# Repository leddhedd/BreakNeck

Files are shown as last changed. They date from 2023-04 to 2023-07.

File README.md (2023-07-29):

# The project formerly known as BreakNeck

<p align="center">
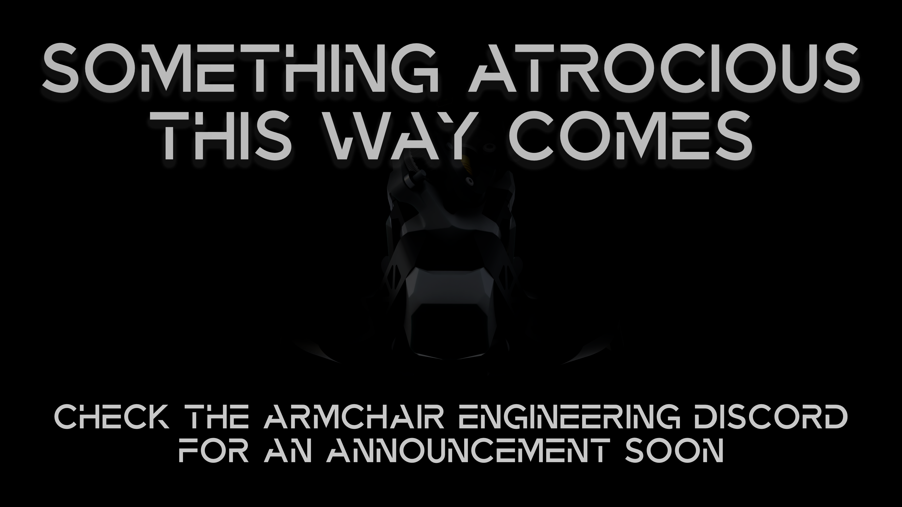
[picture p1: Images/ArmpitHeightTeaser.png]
  
</p>

Check out the Armchair Engineering Discord, and join the Breakneck User-Project ***[HERE](https://discord.com/channels/1029426383614648421/1071214081236816012)***

## THIS PROJECT HAS EVOLVED
BreakNeck is about to move over to the armchair engineering github, as well as undergoing some changes and additions.

## WE STAND ON THE SHOULDERS OF GIANTS

i want to give a particularly huge thanks to DoubleT, aTinyShellScript, Derpimus, Corvid, Zruncho, Maz, Kmobs, Smokescreens, Zackm0n, ohpvp, DWTas, ByThorsThunder, Frank.af, Kyleisah cBon, many of the members of the annex community and team, as well as many others for getting stuck in, test printing parts, and in some particularly idiotic cases, trialing, fitting and using the toolhead. the 3dp community wouldnt be what it is without the contibution and help of individuals like these, and i certainly wouldnt have completed the project to this level of polish without their help.

Huge thanks to all the guys over at the Armchair Engineering, Voron, and Annex discord for all the help and support in bringing this project together.

## What is this?

if you have stumbled across this repo, you are looking at the predecessor to **ARMPITHEIGHT** , i will leave the following description of what Breakneck was below for some back-lore.

Breakneck was a toolhead designed primarily for the Voron ecosystem, and any other front rail, front belt CoreXY Printer.
The main features and testing focus of the toolhead were remote air cooling, and a deliberate bend in the post-extruder filament path, for the purposes of inducing a bowden-like buffering effect.

## [> > > ASSEMBLY GUIDE < < <](https://github.com/leddhedd/BreakNeck/blob/main/Images/Assembly/Assembly-Instructions.md)

<p align="center">
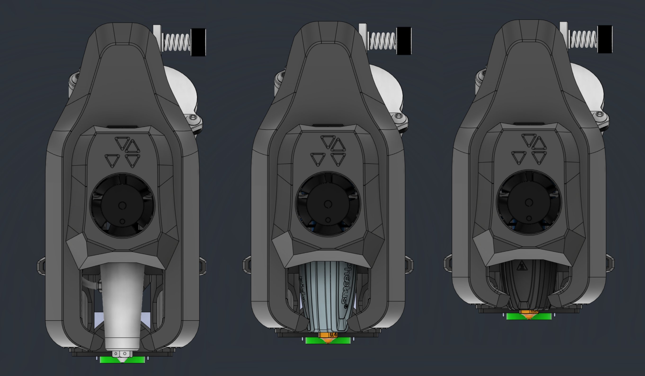
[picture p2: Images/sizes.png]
  
</p>

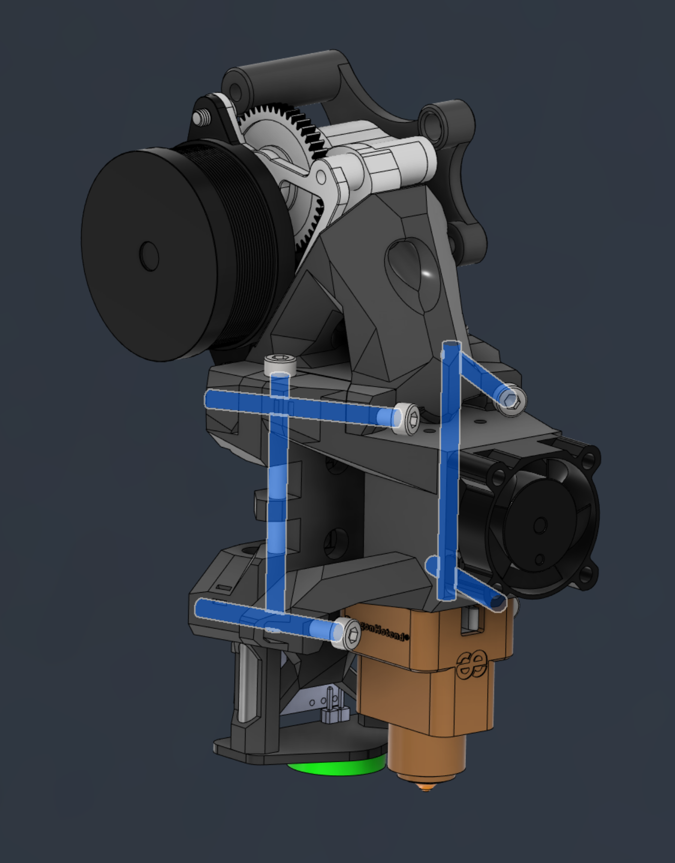
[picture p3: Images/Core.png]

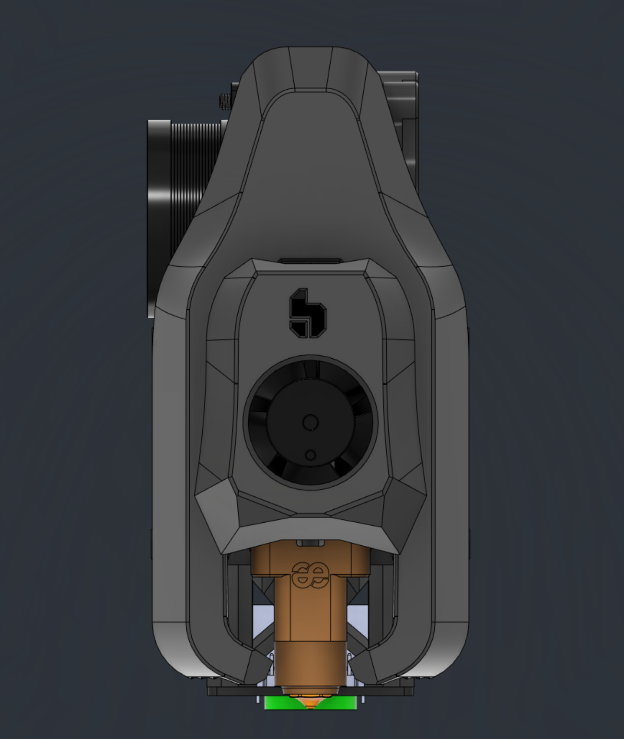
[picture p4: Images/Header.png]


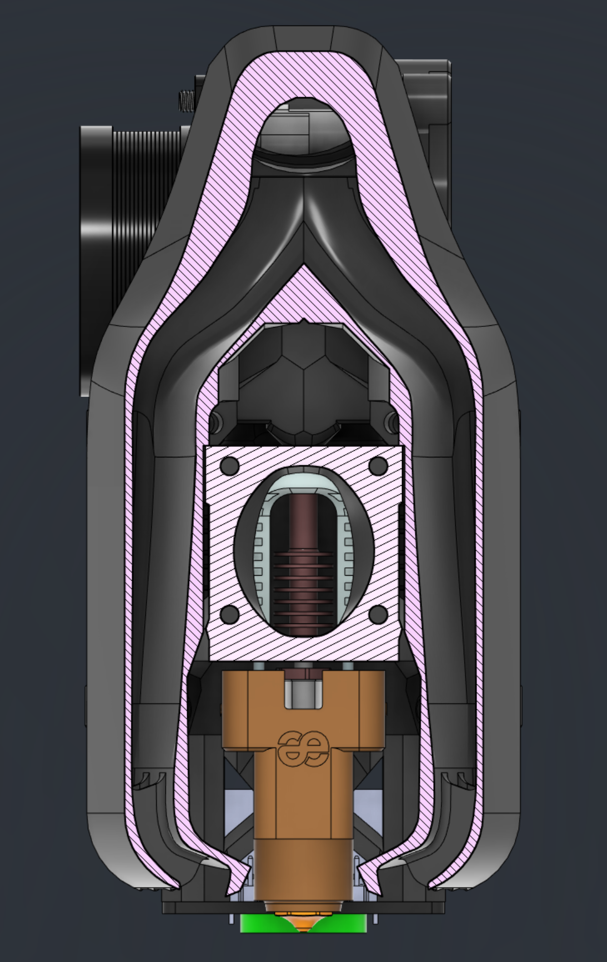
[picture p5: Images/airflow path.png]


Cpap cooling somewhat speaks for itself, its more cooling than you can typically get. more to come with updates, but the project focuses currently on 7040 blower fans commonly avaliable on AliExpress, and looking into small dyson hairdryer blower fans and other BLDC ducted fan options. As development continues, the focus will move away from the toolhead and more toward maximising performance from the remote fan whilst sourcing cheap and openly avaliable parts.

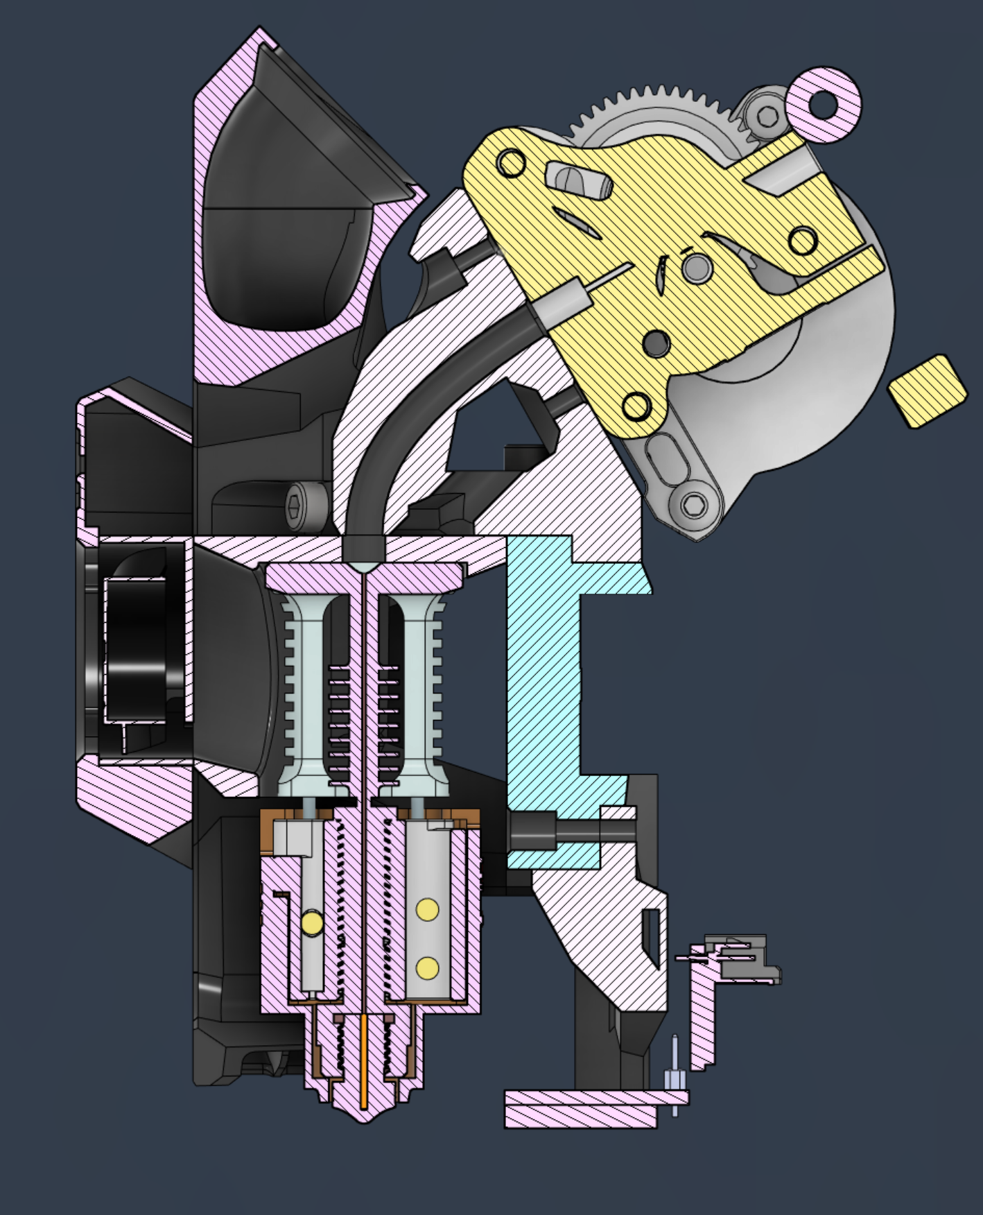
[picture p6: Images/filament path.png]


The post-extruder filament path bend is a solution to 2 problems, first is duct pathing is a nightmare with an extruder directly above the hotend, but most critically, bowden machines have been shown in several examples to produce cleaner walls and prints than direct drive machines. this effect comes at a tradeoff of course, with bowden machines having PA values that are essentially uncontrollable at high speed printing.
the filament path bend aims to create a small buffer of filament between the extruder and the hotend, in order to deliberately increase PA values and reduce the visibility of any extruder artifacting in the extruded lines.
The claims about bowden in general and easy to verify, and 24/7 printing has several videos, as well as MirageC on their efforts to reduce issue6 and VFA artifacting on their prints, with many commenters, and MrageC himself showing how clean a bowden machine can print when looking at this isolated artifact
in testing so far, the breakneck extruder mount seems to be producing a similar effect to the bowden tube, but keeping PA values much more in check than a full bowden system, allowing for more potential quality and less limitations on high-speed printing.

After Breakneck was tested thoroughly for a few months by various wonderful community members, it was decided to up the scope and try to provide the benefits of the above, whilst also providing a ground up toolhead ecosystem that would allow tinkers and builders to easily modify and integrate their hotends,,extruders, and cooling solutions into a hyper-rigid, totally modular, and above all, lightweight and performant toolhead that shed the constraints of older toolheads.

**ARMPITHEIGHT** will debut on the armchair engineering github organisation, and will superceed Breakneck.

## Currently Supported Hardware:
strikethrough is incomplete but planned

### Carriages
- MGN12 6mm Belts
- MGN12 9mm Belts
- MGN9 6mm Belts
- MGN9 9mm Belts

### Extruders
- VZ-Hextrudort
- microsherpa
- Kyro
- ~~DFA~~

### Hotends:
- Goliath - LARGE
- RapidoUHF - Medium
- RapidoHF - Small
- DragonUHF
- ~~Volcmosq/Magnum+~~
- ~~Waterheater~~

### Probes
- Beacon
- Klicky
- Klicky/PCB
- ~~Euclid~~
- ~~TAP~~

More to be added as development continues.

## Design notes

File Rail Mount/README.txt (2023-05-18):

Print all of the STLs in the appropriate carriage folder for your machine. if you are using 6mm belts, print ALL 4 of the stoppers, LU is left upper, LL is left lower, RU is right upper and RL is right lower. install the stoppers on the ends of the belts after inserting them into the belt clamps to prevent them walking up the screws

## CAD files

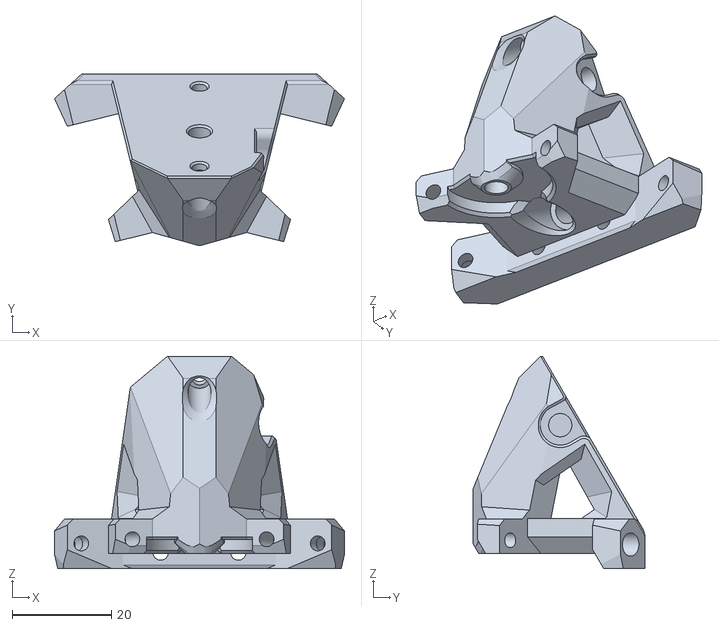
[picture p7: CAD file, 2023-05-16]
Extruder Blocks/BreakNeck_ExtruderBlock_MicroSherpa.stl
58.4 x 34.6 x 42.7

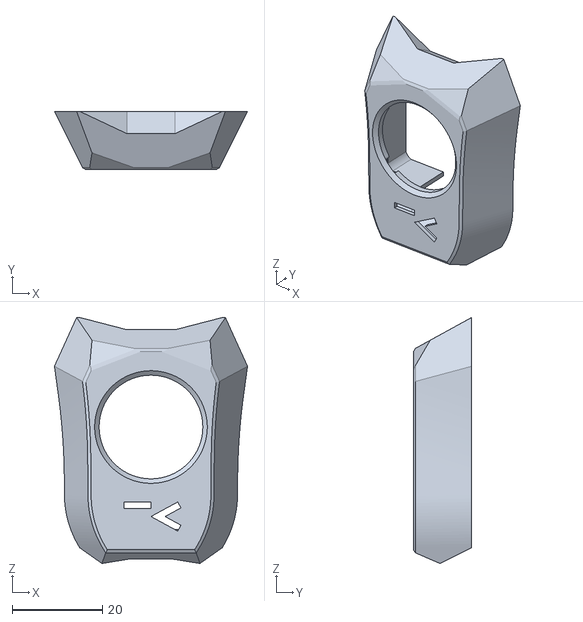
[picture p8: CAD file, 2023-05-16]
Front Cover/BreakNeck_Front_Cover-aTinyShell.stl
42.9 x 12.9 x 54.6

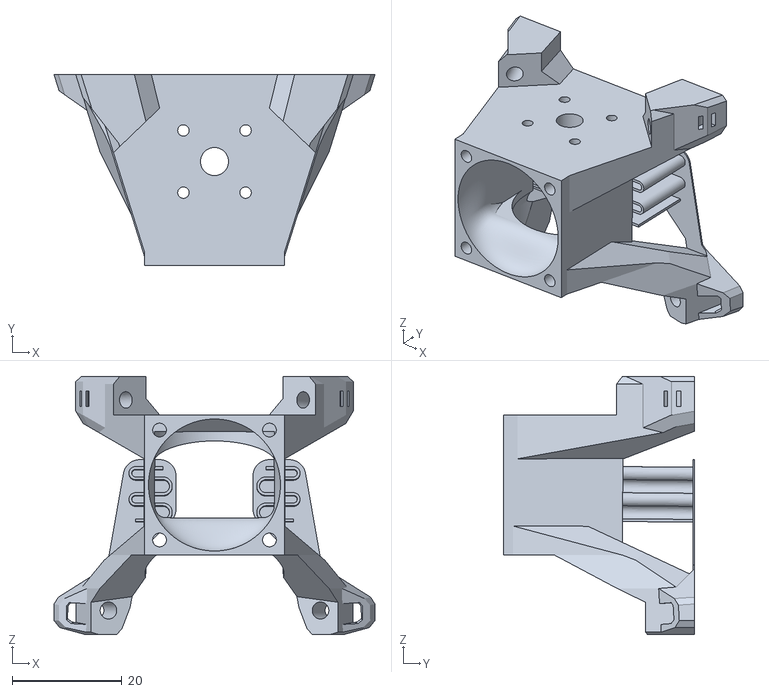
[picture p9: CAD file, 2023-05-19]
Hotend Mount/BreakNeck_Goliath_Hotend_Mount.stl
58.4 x 34.7 x 47.0

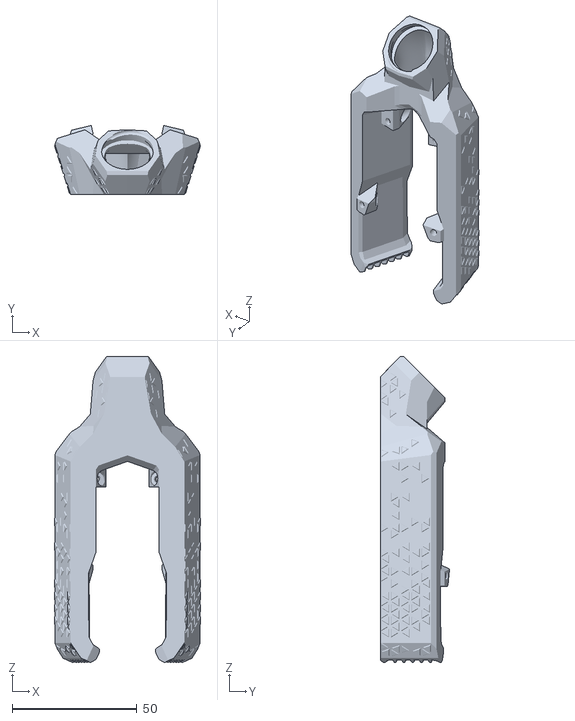
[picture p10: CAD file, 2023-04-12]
Probe Mounts and Ducts/Large/BreakNeck_Ducts_Large.stl
58.6 x 27.8 x 122.8

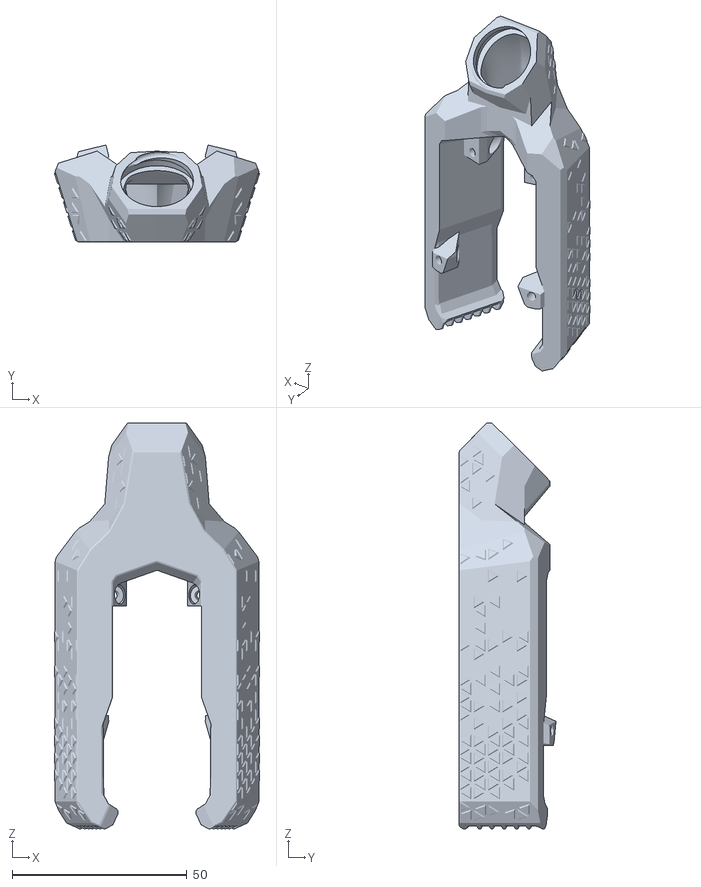
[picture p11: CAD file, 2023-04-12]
Probe Mounts and Ducts/Medium/BreakNeck_Medium_Ducts.stl
58.6 x 27.8 x 116.1

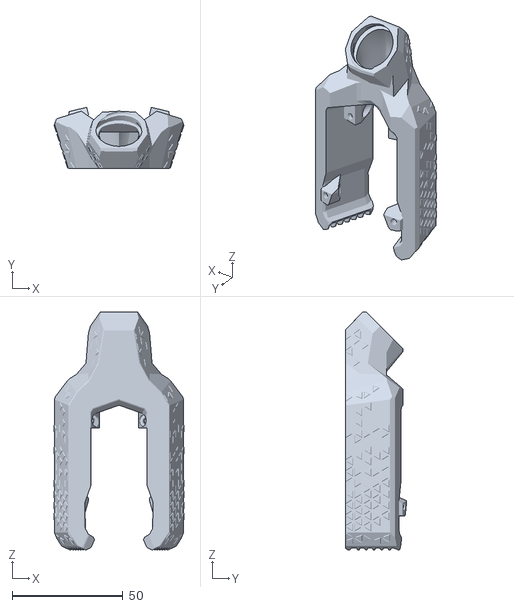
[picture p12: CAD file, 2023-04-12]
Probe Mounts and Ducts/Small/BreakNeck_Small_Ducts.stl
58.6 x 27.8 x 107.5

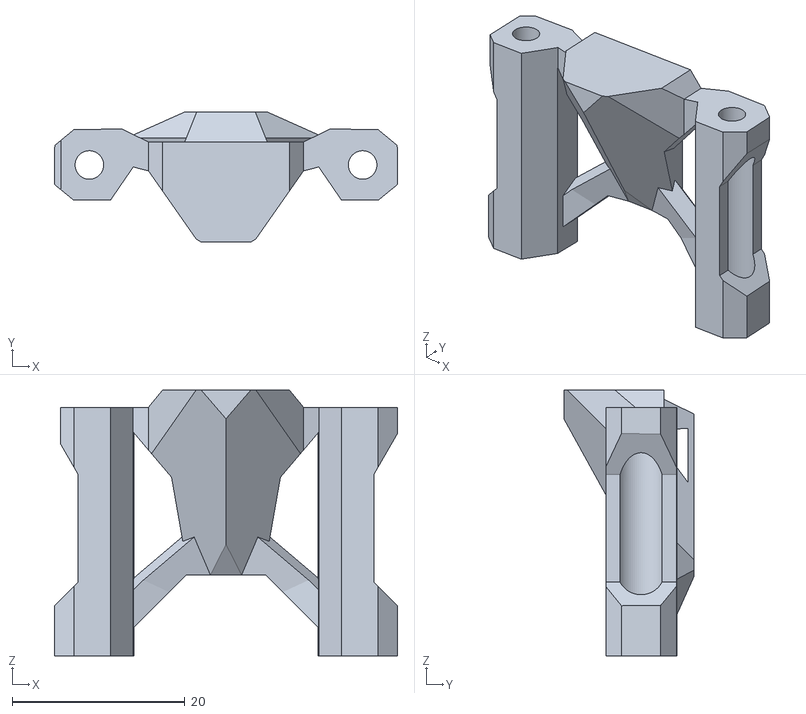
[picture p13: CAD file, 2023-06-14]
Probe Mounts/Beacon/BreakNeck_Probemount_Beacon_Large.stl
39.7 x 15.1 x 30.7

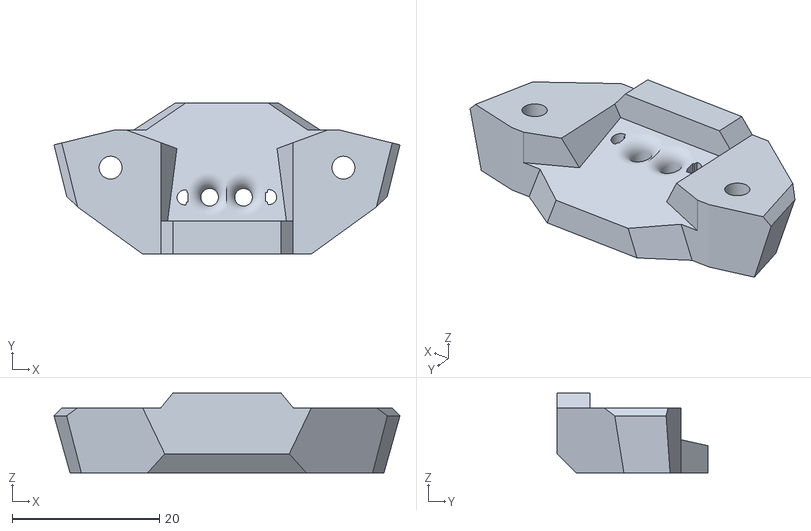
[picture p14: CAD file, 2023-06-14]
Probe Mounts/Klicky/BreakNeck_Probemount_Klicky_Small.stl
46.9 x 20.5 x 10.9

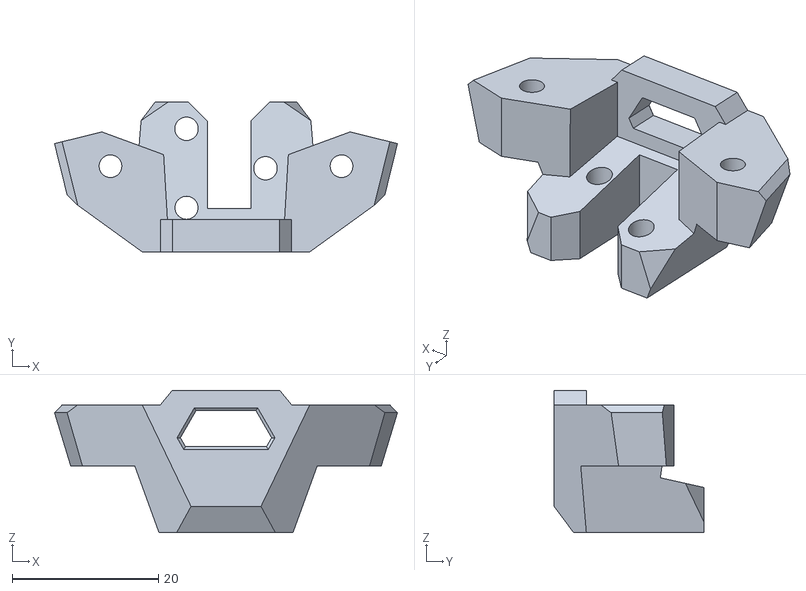
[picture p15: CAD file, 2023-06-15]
Probe Mounts/KlickyPCB/BreakNeck_Probemount_KlickyPCB_Long.stl
46.9 x 20.5 x 19.5

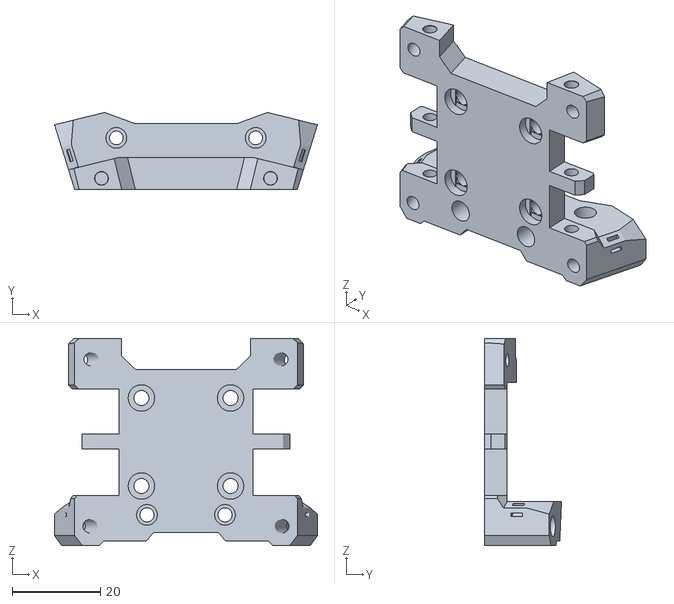
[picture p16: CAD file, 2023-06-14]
Rail Mount/MGN12/Breakneck_RailMount_MGN12.stl
59.6 x 17.5 x 47.0

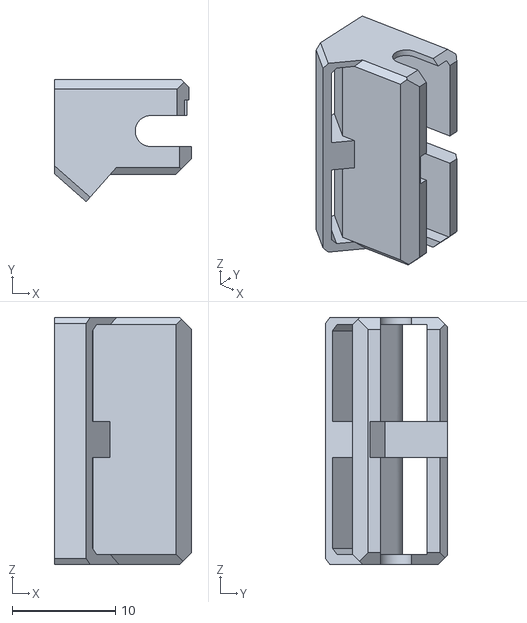
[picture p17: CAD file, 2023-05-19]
Rail Mount/MGN9/Breakneck_RailMount_MGN9-9mm_Clampx2.stl
13.3 x 11.9 x 23.9

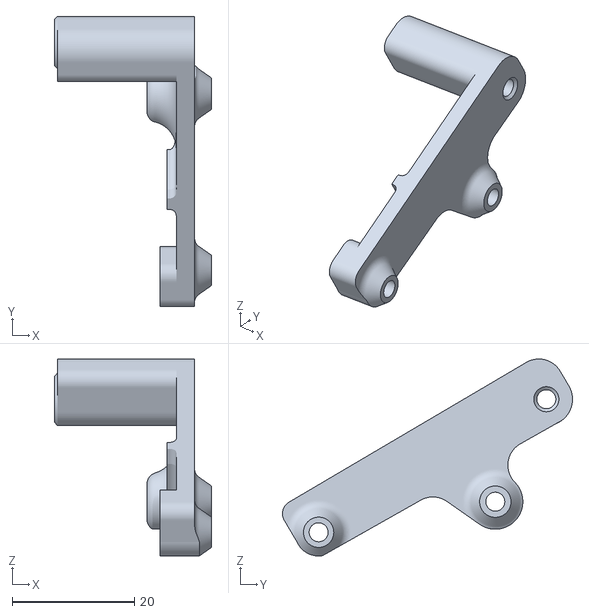
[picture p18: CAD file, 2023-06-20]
Toolhead Board Mounts/BreakNeck_CaribinerMount_Microsherp.stl
25.7 x 47.4 x 32.2

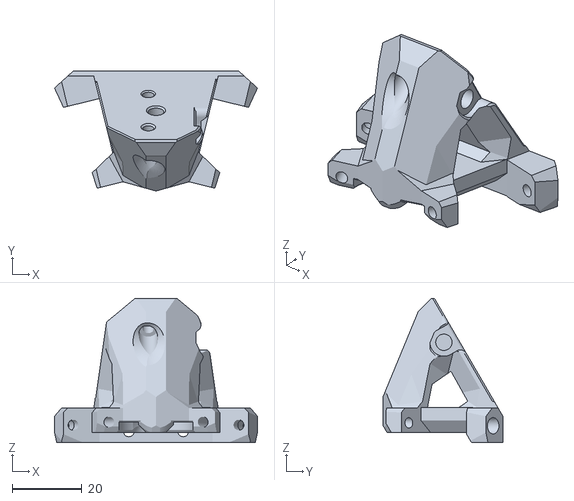
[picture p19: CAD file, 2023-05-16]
Extruder Blocks/BreakNeck_ExtruderBlock_VZ-Hextrudort.stl
58.4 x 34.6 x 41.5

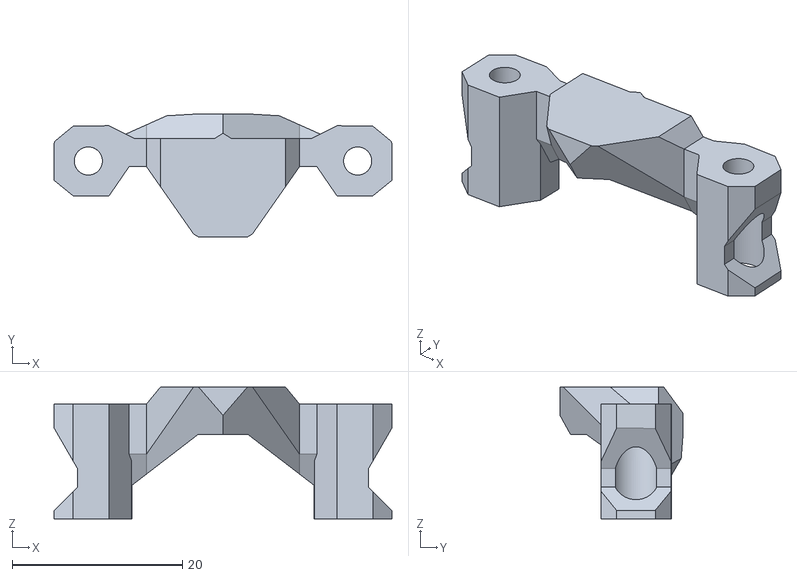
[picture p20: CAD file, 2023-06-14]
Probe Mounts/Beacon/BreakNeck_Probemount_Beacon_Small.stl
39.7 x 14.5 x 15.5

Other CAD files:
Front Cover/BreakNeck_Front_Cover-Leddhedd.stl
Hotend Mount/BreakNeck_Rapido _Hotend_Mount.stl
Probe Mounts/Klicky/BreakNeck_Probemount_Klicky_Medium.stl
Probe Mounts/KlickyPCB/BreakNeck_Probemount_KlickyPCB_Small+Medium.stl
Front Cover/BreakNeck_Front_Cover-DoubleT.stl
Front Cover/BreakNeck_Front_Cover-Tri.stl
Hotend Mount/BreakNeck_DragonUHF _Hotend_Mount.stl
Probe Mounts/Beacon/BreakNeck_Probemount_Beacon_Medium.stl
Probe Mounts/Klicky/BreakNeck_Probemount_Klicky_Long.stl
Rail Mount/MGN12/Breakneck_RailMount_MGN12-6mm_Clampx2.stl
Rail Mount/MGN12/Breakneck_RailMount_MGN12-9mm_Clampx2.stl
Rail Mount/MGN9/Breakneck_RailMount_MGN9-6mm_Clampx2.stl
Rail Mount/MGN9/Breakneck_RailMount_MGN9.stl
Toolhead Board Mounts/BreakNeck_BoardMount_Microsherp.stl
Toolhead Board Mounts/BreakNeck_BoardMount_VZ-Hextrudort.stl

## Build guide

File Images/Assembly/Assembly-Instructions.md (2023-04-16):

# Please follow the below images to assemble your toolhead

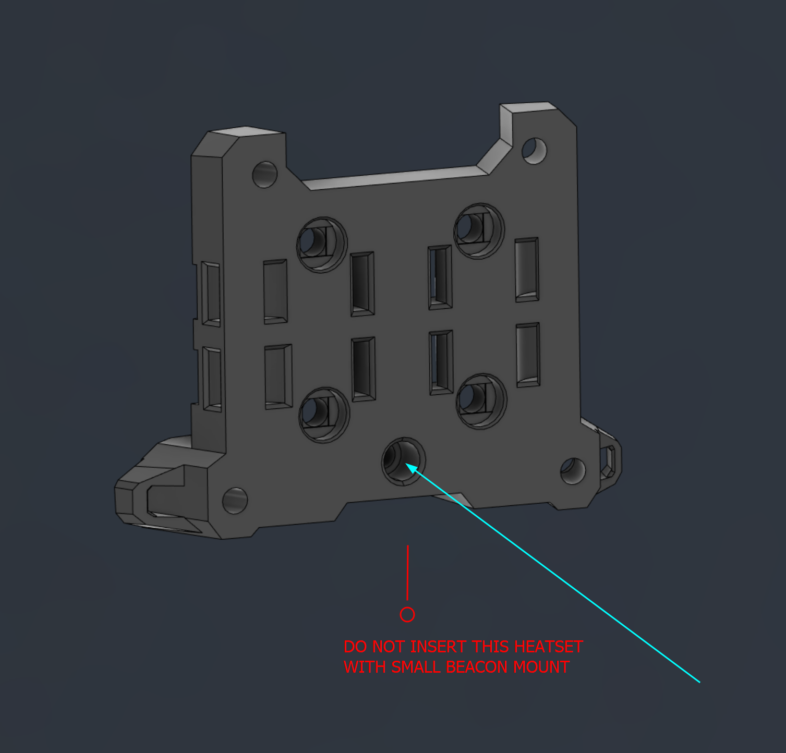
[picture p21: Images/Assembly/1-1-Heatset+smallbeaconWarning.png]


Install a standard heatset into the front of the carraige mount

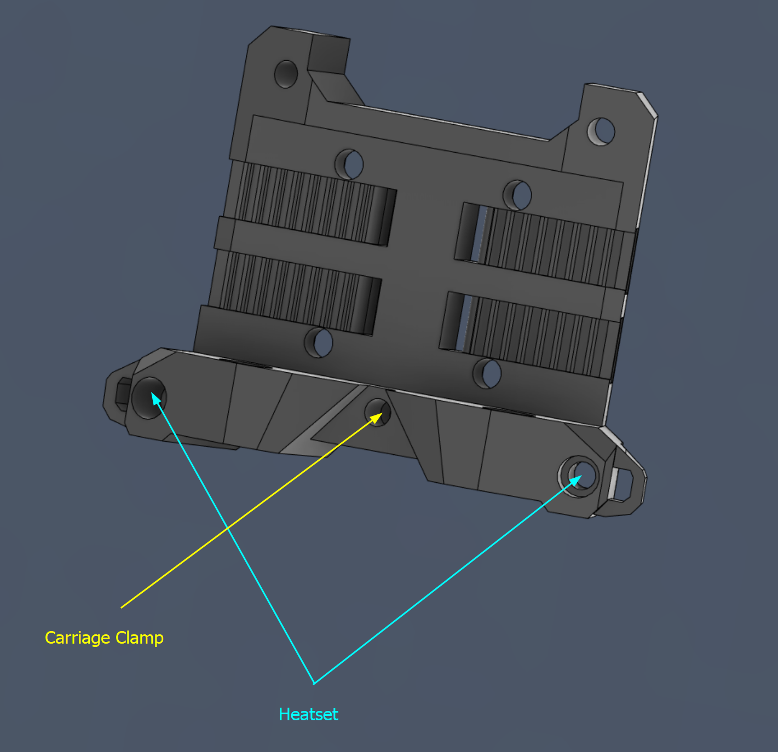
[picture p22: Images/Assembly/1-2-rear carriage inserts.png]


insert a heatset into each of the holes shown, the carriage clamp can be used [EXCEPT WITH SMALL BEACON MOUNT] with an m3 SHCS with an m4 washer on it, loosely installed until after mounting to the rail carriage

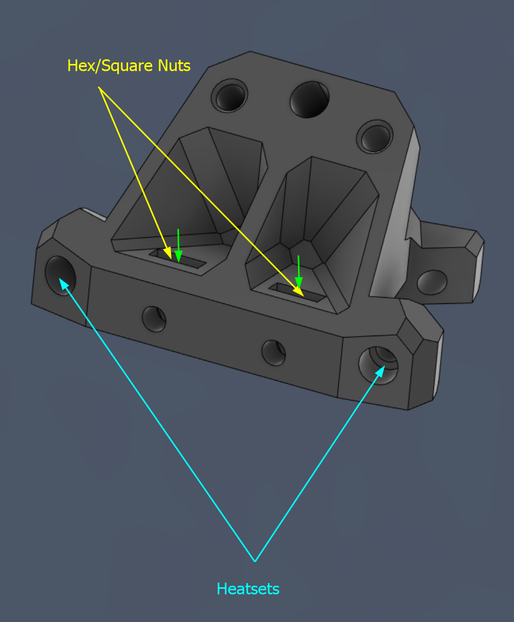
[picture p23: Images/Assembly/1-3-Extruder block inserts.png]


Insert a heatset into each of the highlighted holes above, square or hex nuts can be inserted into the yellow holes, and used in the same manner as the carriage clamp, with an m3SHCS and an m4 washer. once installed onto the rail carriage these can be tightened down to clamp onto the rail carriage more securely

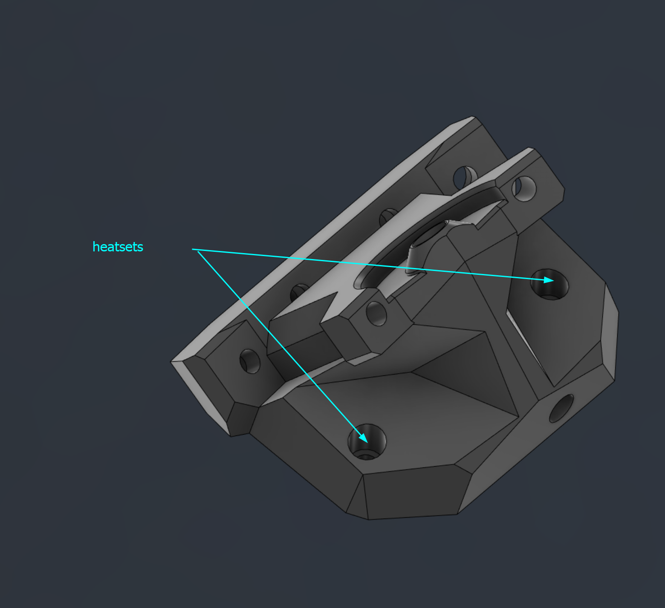
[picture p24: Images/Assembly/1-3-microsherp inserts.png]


**MICROSHERPA ONLY  ^^^^** insert heatsets into the front of the microsherpa block if using this part

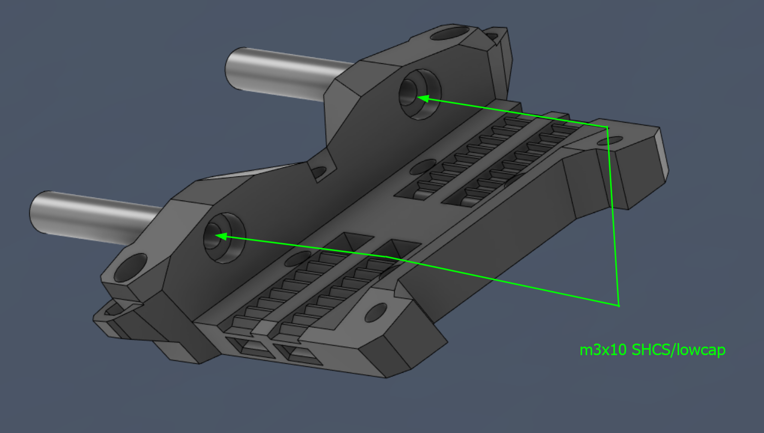
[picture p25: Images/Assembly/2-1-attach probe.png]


use the appropriate length aluminium standoffs to attach to the m3 screws inserted into the bottom of the rail carraige. ensure no part of the screw head is proud of the top surface, or it will interfere with rail mounting.

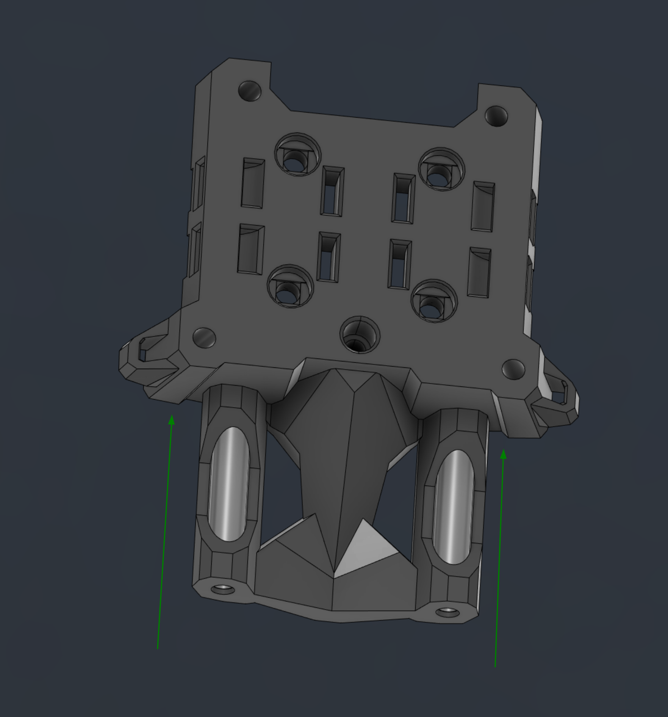
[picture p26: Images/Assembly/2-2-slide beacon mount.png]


slide the beacon probe mount over the aluminium standoffs

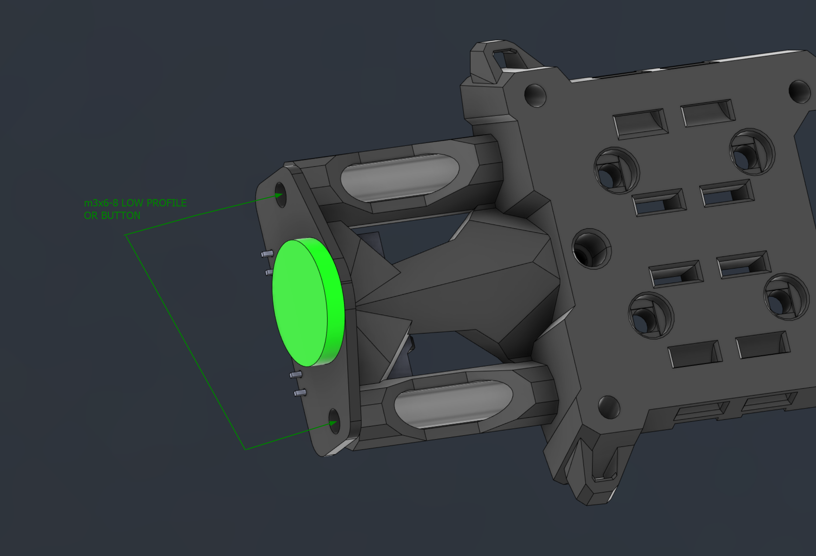
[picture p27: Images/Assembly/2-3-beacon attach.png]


attach the beacon to the bottom of the standoffs, ensuring to use LOW PROFILE or BUTTON HEAD screws. anything with a larger head **MAY HIT YOUR BED!!!!!!**

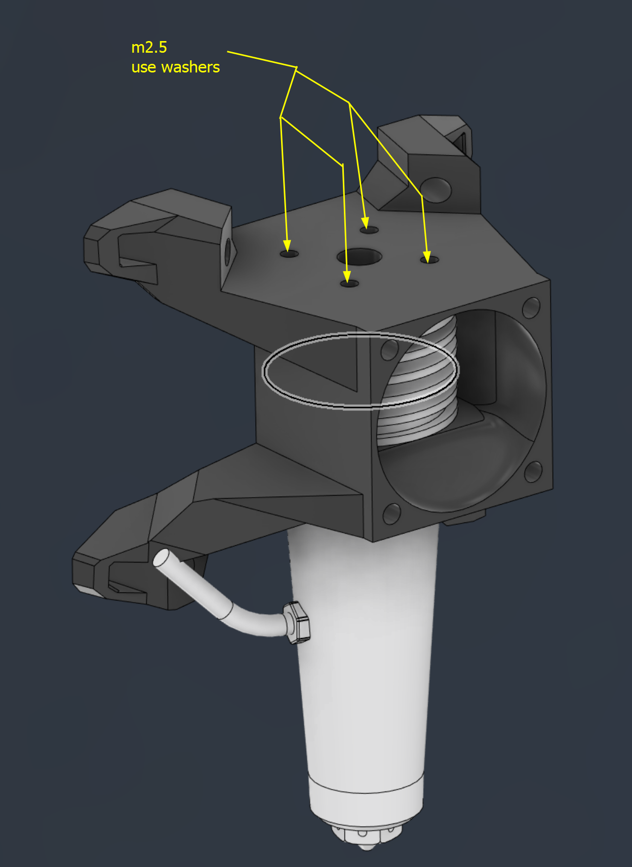
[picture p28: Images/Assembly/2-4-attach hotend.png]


install the appropriate length m2.5 screws for your hotend, preferably using m3 or m2.5 washers to spread the load over the top surface

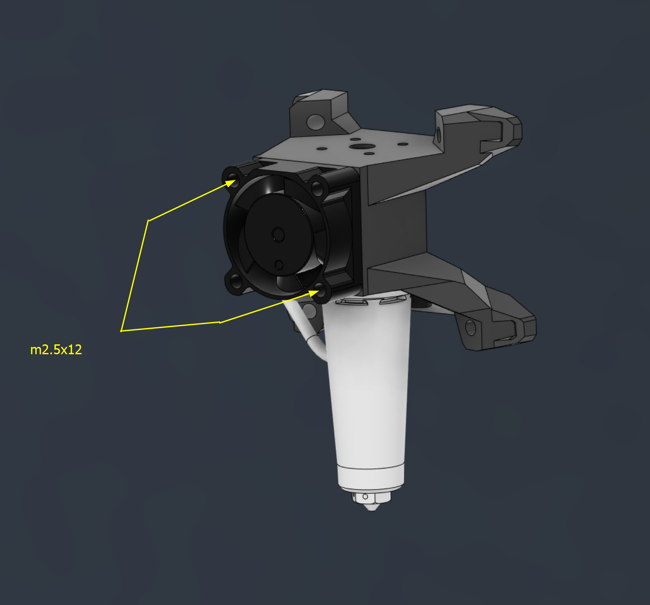
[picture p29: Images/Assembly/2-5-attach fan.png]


install the front fan using 2 or 4 m2.5 screws

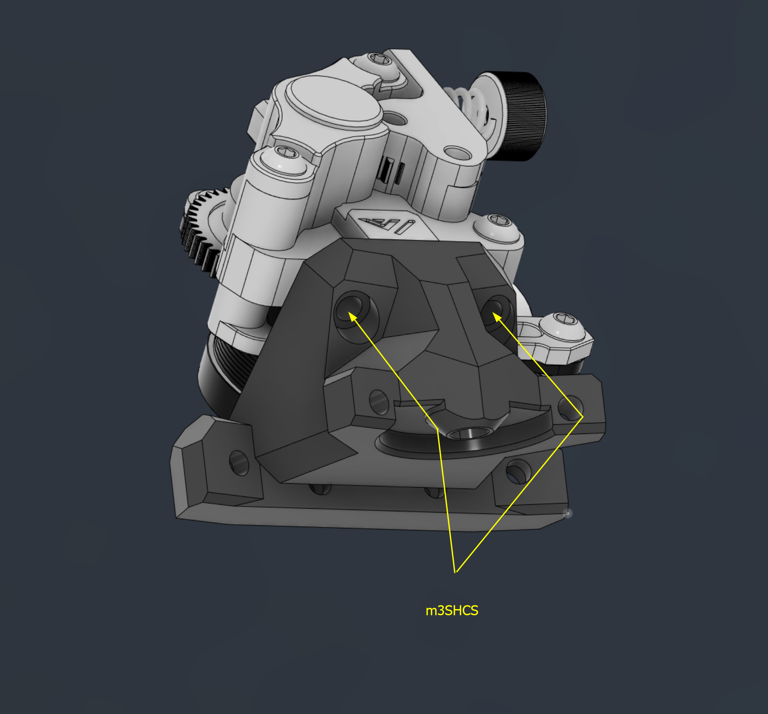
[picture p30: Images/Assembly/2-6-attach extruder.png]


mount your extruder to the appropriate block. Hextrudort screws into the extruder from the front, microsherpa screws into the heatsets from the top of the extruder down

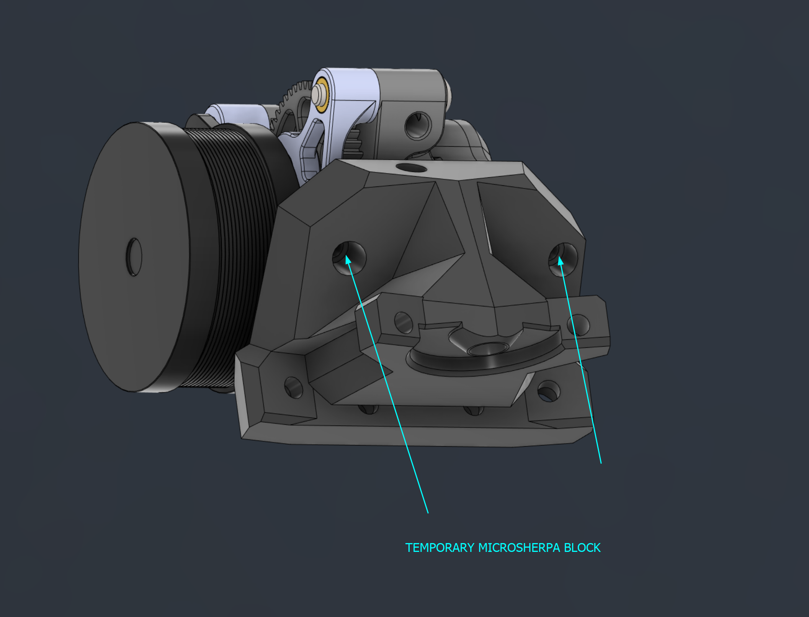
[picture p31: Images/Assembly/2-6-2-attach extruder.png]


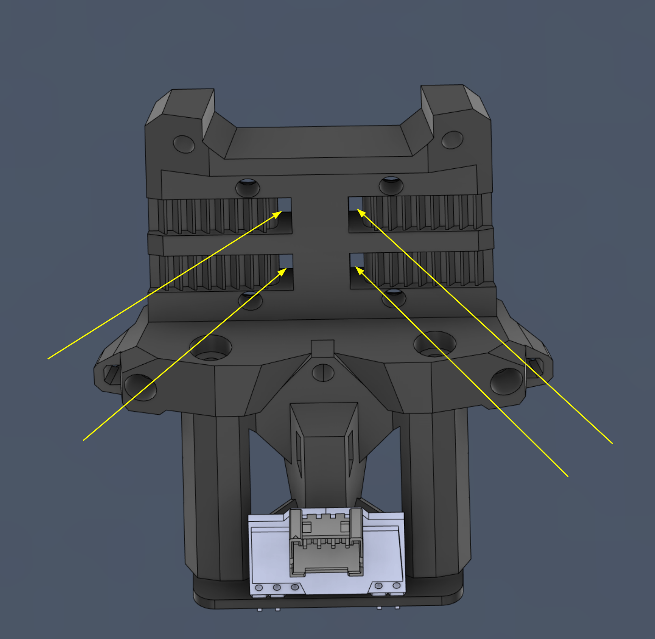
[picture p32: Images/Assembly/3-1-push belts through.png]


Push your belts through the holes in the rear carriage facing side of the carriage mount, ensuring that the teeth of the belt sit into the recesses on the back

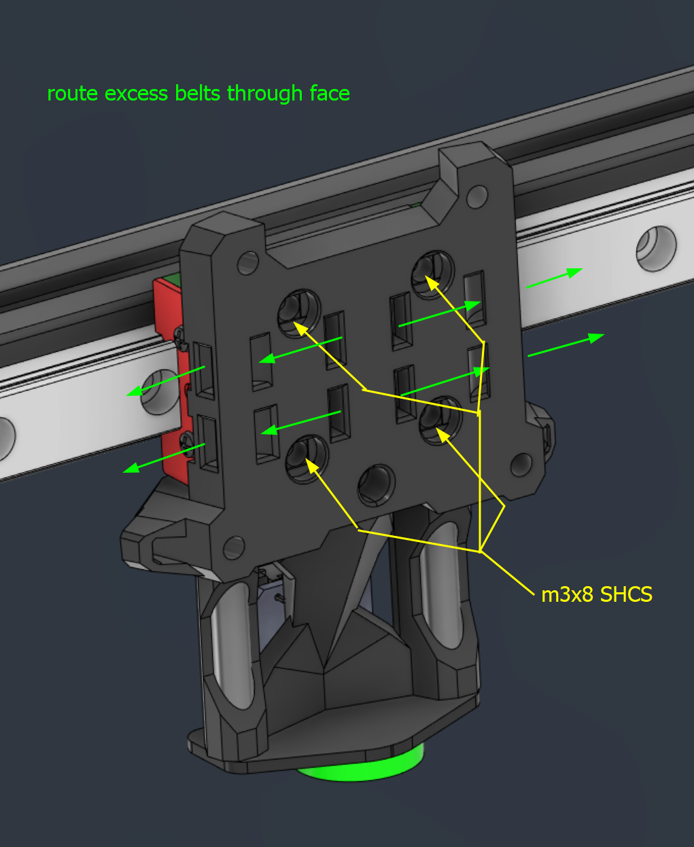
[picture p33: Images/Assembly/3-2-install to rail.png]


place the carriage mount over the rail carriage, pull your belts tight through the part, and push any excess belt through the outside holes in the face, with the ends coming out the sides of the carriage.

secure the part to the rail with the 4 m3 SHCS , ensuring all belts are equal length and secured properly. you can at this point tighten the carriage clamp screw above the probe mount on the rear bottom of the rail carriage.

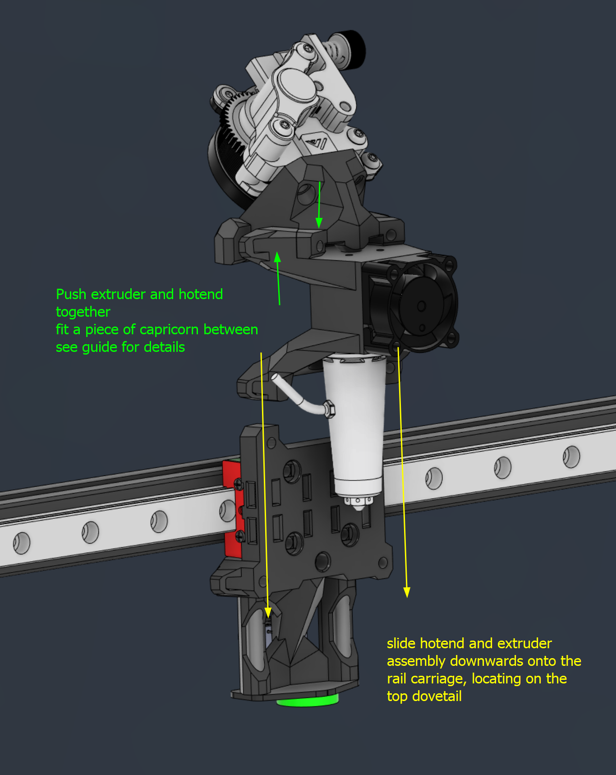
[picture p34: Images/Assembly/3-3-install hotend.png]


push the hotend and extruder blocks together as shown, and slide the assembly down over the rail carraige, making sure the screw holes align. you may cable tie the wiring at this stage, and all wires should only be attached to the block that their corresponding parts are attached to, allowing for easy dissasembly without cutting cable ties

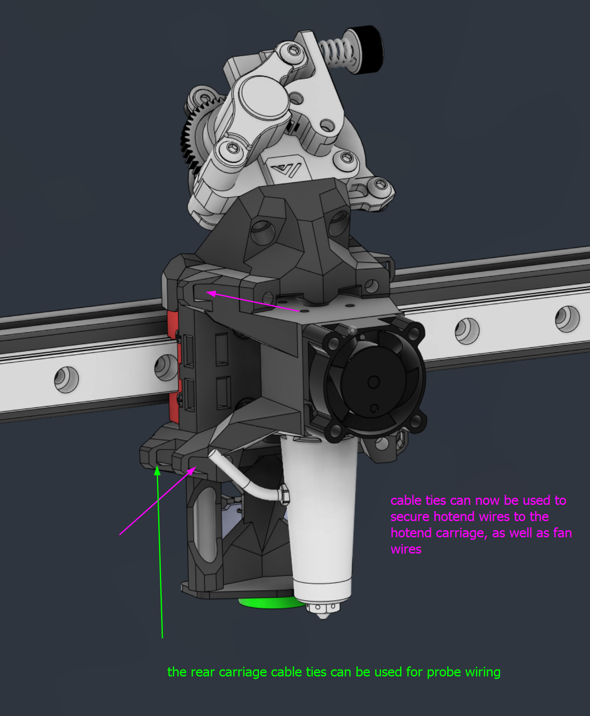
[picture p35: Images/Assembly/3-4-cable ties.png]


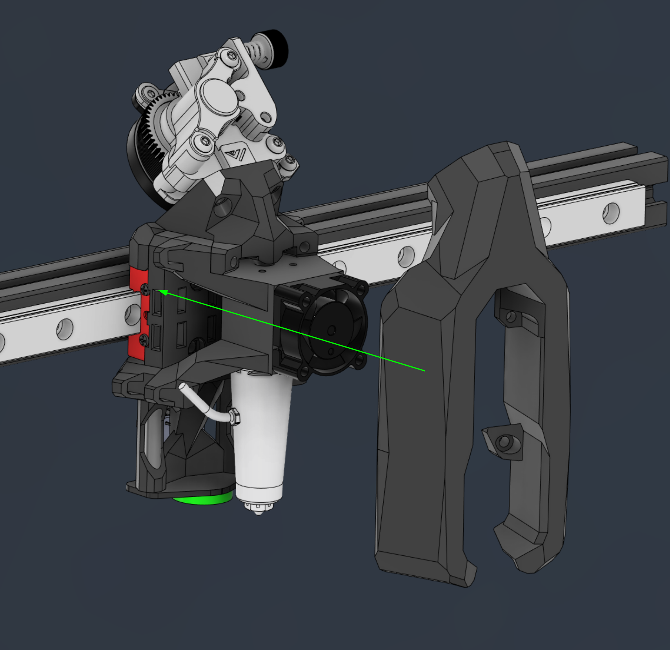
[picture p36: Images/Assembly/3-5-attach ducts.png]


slide the ducts straight backwards over the assembly

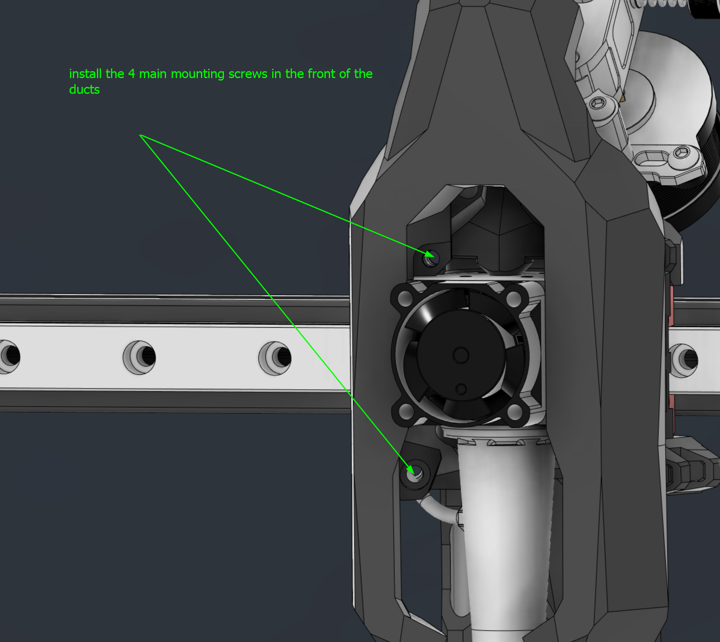
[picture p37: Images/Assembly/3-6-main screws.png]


insert all 4 main mounting screws into the front of the duct, taking care not to cross thread things. the screw axis are deliberately out of alignment with the major axis, so the screws will locate at a slightly wonky angle going in, look through the front of the hole and firmly screw everything together.

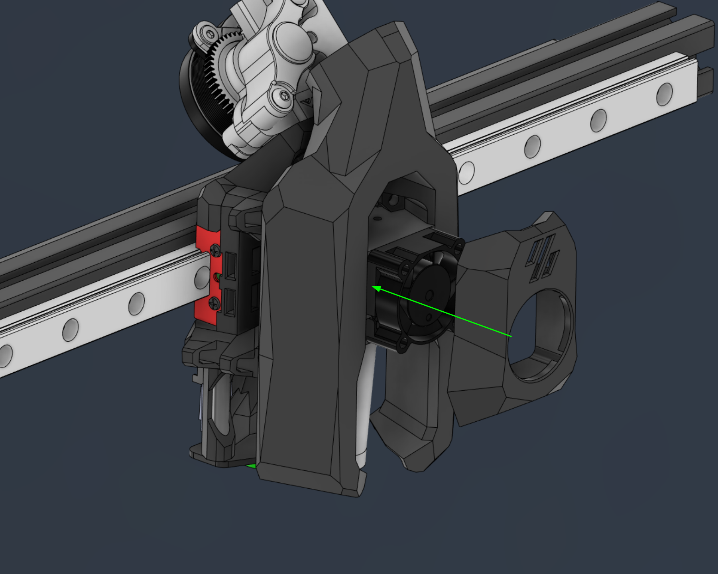
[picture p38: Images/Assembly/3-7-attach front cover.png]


Push the front cover over the 2510 fan. this is just a slip fit and holds on with friction

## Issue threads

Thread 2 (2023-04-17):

Beacon Normal orientation support

thiagolocatelli, 2023-04-17:
The current beacon mount does not have enough clearance for the beacon pcb.

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

leddhedd, 2023-04-17:
Clearance for the standard beacon orientation will be a problem on all 3 mounts, will make adjustments to allow for either to be used

Closed 2023-04-19.

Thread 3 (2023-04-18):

ebb36 board incompatible with flysht mount

leddhedd, 2023-04-18:

Closed 2023-05-18.

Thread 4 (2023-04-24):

Rapido wire management issues

leddhedd, 2023-04-24:
Strain relief on rapido is awkward, redesign to rear spar on hotend mounts required

Closed 2023-05-18.

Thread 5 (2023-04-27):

Front Cover loose

leddhedd, 2023-04-27:
front cover needs cleareances for m2.5 shcs and tabs to retain during fast printing, need to check IS too

Closed 2023-07-29.

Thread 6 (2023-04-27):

Hose comes loose during high speed moves

leddhedd, 2023-04-27:
hose requires positive retention with grub screw and rib

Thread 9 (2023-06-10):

MGN12H Rail mount incompatible with beacon mount

RefractingPrism, 2023-06-10:
The MGN12H mount is incompatible with the small duct beacon mount. The mgn12h rail mount is missing the triangular cutout for proper fitment.

leddhedd, 2023-06-14:
sorry yes, ill update that part now, however it important to note that the small beacon mount cannot be used with the carraige clamping screws that go through the carriage piece

RefractingPrism, 2023-06-14:
just to clarify this was the section of the probe mount that conflicts with the carriage mount.
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

I guess im having trouble following which screws make it not compatible.

leddhedd, 2023-06-14:
yes sorry, that just needs entirely removing, just pointing out that the two holes in the front of the carraige there below the rail mounting screws need to be empty, if you put the heatsets in there, they are technically in the beacon exclusion zone

im just updating that part now, should be on the repo in a few minutes

leddhedd, 2023-06-14:
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
these two holes here, im uploading the updated beacon probe mounts, as well as updated probe mounts for everything that should all now be compatible with the new carriages, apologies for the inconvinience on that one

RefractingPrism, 2023-06-16:
Thanks for following up, i didnt think of the exclusion zone but that makes sense now!

Closed 2023-07-29.

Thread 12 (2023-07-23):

CAD Access

brianvoe, 2023-07-23:
I love the idea and want to try it out but wanted to try a couple of alternative changes. Any chance you can share the CAD files?

leddhedd, 2023-07-29:
Breakneck is getting a bit of an overhaul, hence the slow progress updates, but once that is released, which should be pretty soon, there will be CAD avaliable for people to mess around with there :)

brianvoe, 2023-07-29:
ok cool thanks for the update!

Closed 2023-07-29.

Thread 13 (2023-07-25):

Make the duct a structural part of the toolhead?

ganzgustav22, 2023-07-25:
It looks heavy, maybe make the duct a structural part of the toolhead, so that the other structural parts can be omitted or made lighter.

leddhedd, 2023-07-25:
you should put the files into  a slicer and check the weight first ^^ looks are decieving :)

Closed 2023-07-29.

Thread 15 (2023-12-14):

Probe Support Request

cplmayo, 2023-12-14:
This sensor is similar to the Beacon but supports CanBus. I have one and am willing to help any way I can.

https://github.com/markniu/Bed_Distance_sensor

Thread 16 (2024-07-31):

Goliath Hotend Support/LGX Support - CAD Files Also Yo

KhaymKhaym, 2024-07-31:
Looking for Goliath hotend support and LGX Lite extruder support. Also support for water block cooling for the Goliath and Chube.

Willing to design this, but I need those STEP files homie.

Love,

KK

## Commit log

2023-04-05 added STLs
    added initial STLs in prep for BETA
    [BreakNeck_Ducts_Large.stl, BreakNeck_ExtruderBlock_VZ-Hextrudort.stl, BreakNeck_Goliath_Hotend_Mount.stl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]
2023-04-05 Create Breakneck_RailMount_MGN12-v2-Sqaure Nuts.stl
    [Breakneck_RailMount_MGN12-v2-Sqaure Nuts.stl]
2023-04-05 added heatset probe mount
    [Breakneck_RailMount_MGN12-v2-Heatset.stl, Breakneck_RailMount_MGN12-v2-Sqaure Nuts.stl]
2023-04-10 fixed rear microsherpa hex slots to 2.5mm and square
    [BreakNeck_ExtruderBlock_MicroSherpa.stl]
2023-04-11 Create BreakNeck_Small_Ducts - No Elephants.stl
    [BreakNeck_Small_Ducts - No Elephants.stl]
2023-04-11 Updated Large components with revised lower screw positions
    [BreakNeck_Ducts_Large.stl, BreakNeck_Goliath_Hotend_Mount.stl, BreakNeck_Probemount_Beacon_Large.stl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]
2023-04-12 Adjusted for new screw pattern
    [BreakNeck_Ducts_Large.stl, BreakNeck_ExtruderBlock_MicroSherpa.stl, BreakNeck_ExtruderBlock_VZ-Hextrudort.stl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]
2023-04-12 Updated Small and Medium Ducts for new screw pattern
    [BreakNeck_Medium_Ducts.stl, BreakNeck_Small_Ducts - No Elephants.stl, BreakNeck_Small_Ducts.stl]
2023-04-12 missed chamfer + tube thread
    [BreakNeck_Medium_Ducts.stl, BreakNeck_Small_Ducts.stl]
2023-04-14 clearance for rapido screws
    [BreakNeck_ExtruderBlock_MicroSherpa.stl, BreakNeck_ExtruderBlock_VZ-Hextrudort.stl]
2023-04-14 more clearance
    [BreakNeck_ExtruderBlock_MicroSherpa.stl, BreakNeck_ExtruderBlock_VZ-Hextrudort.stl]
2023-04-14 added test duct and front cover, fixed beacon mount standoffs
    [BreakNeck_Front_Cover_TEST.stl, BreakNeck_Probemount_Beacon_Large.stl, BreakNeck_Probemount_Beacon_Medium.stl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]
2023-04-15 Printability Tweaks, more test ducts
    [BreakNeck_ExtruderBlock_MicroSherpa.stl, BreakNeck_ExtruderBlock_VZ-Hextrudort.stl, BreakNeck_Front_Cover_TEST.stl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]
2023-04-15 missed chamfers
    [BreakNeck_ExtruderBlock_MicroSherpa.stl, BreakNeck_ExtruderBlock_VZ-Hextrudort.stl]
2023-04-15 More printability Tweaks
    [BreakNeck_Goliath_Hotend_Mount.stl, BreakNeck_Rapido _Hotend_Mount.stl, Breakneck_RailMount_MGN12-v2-Heatset.stl]
2023-04-16 added assembly instruction images
2023-04-16 rename assembly
2023-04-18 Updated all duct sizes to new v2 duct geometry and styling
2023-04-18 added supports to hotend mounts
    [BreakNeck_Goliath_Hotend_Mount.stl, BreakNeck_Rapido _Hotend_Mount.stl]
2023-04-18 New front cover
    [BreakNeck_Front_Cover.stl, BreakNeck_Front_Cover_TEST.stl]
2023-04-18 fixed fitment
    [BreakNeck_ExtruderBlock_ROTATED_MicroSherpa.stl]
2023-04-18 fixed medium beacon mount standoff clearance
    [BreakNeck_Probemount_Beacon_Medium.stl]
2023-04-18 printability for ducts, better front cover, added microsherpa toolhead board plate
    [BreakNeck_BoardMount_Microsherp.stl, BreakNeck_BoardMount_VZ-Hextrudort.stl, BreakNeck_Front_Cover.stl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]
2023-04-18 added rotated hextrudort parts
    [BreakNeck_BoardMount_ROTATED_VZ-Hextrudort.stl, BreakNeck_ExtruderBlock_ROTATED_VZ-Hextrudort.stl]
2023-04-19 updated beacon mount to work with either variant
    [BreakNeck_Probemount_Beacon_Large.stl, BreakNeck_Probemount_Beacon_Medium.stl, BreakNeck_Probemount_Beacon_Small.stl]
2023-04-19 better bridging
    [BreakNeck_Probemount_Beacon_Large.stl, BreakNeck_Probemount_Beacon_Medium.stl]
2023-05-16 Updated all printable parts to Beta 1 state
    new parts uploaded, upper screws have been angled more to make them splay more at the back, and interlock with the new rail carriage belt screws
    Added support for Klicky S,M,L , KlickyPCB S+M,L, new beacon mounts, Dragon UHF support, and other printability and strength tweaks
    [BreakNeck_DragonUHF _Hotend_Mount.stl, BreakNeck_ExtruderBlock_MicroSherpa.stl, BreakNeck_ExtruderBlock_ROTATED_MicroSherpa.stl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]
2023-05-18 updated for new carriage and belt clamps
    [Breakneck_RailMount_MGN12-6mm.stl, Breakneck_RailMount_MGN12-9mm.stl, Breakneck_RailMount_MGN12-LeftBelt.stl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]
2023-05-18 added 6mm belt stoppers
    insert these stoppers after installing 6mm belts to keep them vertically constained
    [6mm Stopper LL.stl, 6mm Stopper LU.stl, 6mm Stopper RL.stl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]
2023-05-18 Re-worked carriages and belt clamping
    [6mm Stopper LL.stl, 6mm Stopper LU.stl, 6mm Stopper RL.stl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]
2023-05-19 Update Carriages, Clamps + HE Mounts
    new carriages with stronger screw holding, better belt clamps with excess routing, adjusted lower legs of hotend mounts for clearance
    [BreakNeck_DragonUHF _Hotend_Mount.stl, BreakNeck_Goliath_Hotend_Mount.stl, BreakNeck_Rapido _Hotend_Mount.stl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]
2023-06-01 reworked mgn12 carriage
    [BreakNeck_Probemount_Beacon_Medium.stl, Breakneck_RailMount_MGN12-6mm_Clampx2.stl, Breakneck_RailMount_MGN12.stl]
2023-06-14 large klicky probe fix
    [BreakNeck_Probemount_Beacon_Medium.stl, BreakNeck_Probemount_Klicky_Long.stl, Breakneck_RailMount_MGN12.stl]
2023-06-14 fixed klicky probes for new carriage
    [BreakNeck_Probemount_Klicky_Medium.stl, BreakNeck_Probemount_Klicky_Small.stl]
2023-06-14 updated beacon mounts for new carriage
    [BreakNeck_Probemount_Beacon_Large.stl, BreakNeck_Probemount_Beacon_Small.stl]
2023-06-14 updated klicky mounts for new carriage
    [BreakNeck_Probemount_Klicky_Medium.stl, BreakNeck_Probemount_Klicky_Small.stl]
2023-06-15 Updated KlickyPCB to new carriage specs
    [BreakNeck_Probemount_KlickyPCB_Long.stl, BreakNeck_Probemount_KlickyPCB_Small+Medium.stl]
2023-06-20 added microsherpa caribiner mount
    [BreakNeck_CaribinerMount_Microsherp.stl]
2023-07-29 ArmPitHeight Teaser
    [BreakNeck_Front_Cover-A.stl]
2023-07-29 removed incorrect filestructure
    [BreakNeck_Front_Cover-A.stl]
